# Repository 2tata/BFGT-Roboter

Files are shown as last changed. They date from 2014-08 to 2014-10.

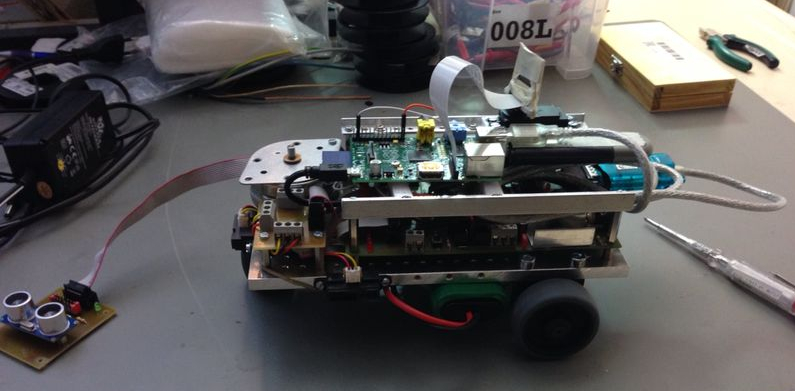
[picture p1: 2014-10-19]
Documentation/Hans Riegel Preis/images/image_47.jpeg

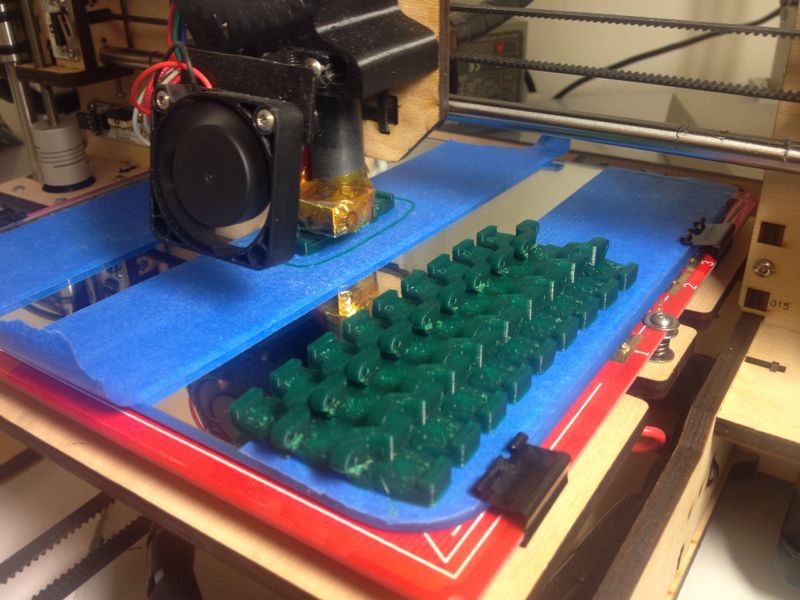
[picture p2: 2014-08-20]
Bilder/BFGT-Roboter_v2/IMG_0849.JPG

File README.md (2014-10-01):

BFGT-Roboter
============

##### ToDo

###### ATmega32
1.Ultraschall-Sensor Funktion inplementieren	  <-- Done, testing

2.Schrittmotor Funktion inplementieren	      	<-- Done, testing

3.Schrittmotor endstop Funktion inplementiren	<-- Done, testing

4.IR Sensoren Funktion korigiren(inplementiren)<-- Done

5.Powersavemode überarbeiten und prüfen	      <-- Done

###### Serial interface
6.Serial daten übertragung optimiren (möglichts kleine und wenige daten)

7.Motor checksum prüfung

###### Raspberry Pi
8.Installations skript coden

9.Open wlan detecter coden

10.Kammera Stream optimiren

11.Servo Steuerung in C

12.Steuerung optimiren

13.Infrarot Leds um die Kamera setzen und über einen Transistor dimbar machen.

14.(OpenCV personen erkennung)

15.Mikrofon audio übertragung

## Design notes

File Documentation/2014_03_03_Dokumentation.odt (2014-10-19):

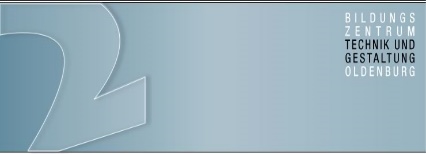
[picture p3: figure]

| Projektkurs - Dokumentation | Schüler: Theis Ammermann, Jan-Tarek Butt, Tobias Beyer, Sören Janke | Klassse: BFI 2
| | | Datum: 11.03.2014

Inhaltsverzeichnis:

1. Einleitung
1. Projektdurchführung
2. Reflexion
3. Literaturverzeichnis
4. Anhang
  a. Protokoll
  b. Zusätzliches Material

Einleitung:

Das Ziel war es, den Mikrocontroller des BZTG's über WLAN/UMTS anzusteuern. Um das sichtbar zu machen, wurde der Mikrocontroller mit Rädern ausgestattet, sodass man ihn über das Internet als eine Art ferngesteuertes Auto ansteuern kann. Das Auto soll vorwärts, rückwärts, nach links und nach rechts fahren können. Der Mikrocontroller wird mit einem Raspberry PI ausgestattet, um mit diesem bestimmte Feature, unter anderem auch die Ansteuerung über das Internet zu ermöglichen.

Erfahrungen hat unsere Gruppe bereits reichlich gesammelt, jeder aus der Gruppe hat Grundkenntnisse in der passenden Programmiersprache „AVR Studio 6“, allerdings gibt es hier natürlich Aufteilungen in unserer Gruppe, den die einen sind gut im Programmieren und die anderen haben bessere Erfahrungen im Bereich deutsch, was bei der Dokumentation hilft.

Das Projekt wird zum Teil außerhalb des Unterrichts bearbeitet. In dem Fach Projektkurs, welches 2-mal pro Woche belegt wird, werden organisatorische Besprechungen und Planungen durchgeführt, außerdem wird an der Dokumentation und an der Programmierung gearbeitet. Außerhalb des Unterrichts werden zum Beispiel Komponenten zum Mikrocontroller hinzugefügt.

Als Software verwenden wir „AVR STUDIO 6.1“ zur „C“ Programmierung des Mikrocontrollers, des weiteren wurden auf dem Raspberry PI die Programmiersprache „Python“ und die Script-Sprache „Bash“ verwendet. Zum Festhalten der Protokolle und der Dokumentation verwendeten wir Microsoft Word und Libre Office. Zum Erstellen der Projektstrukturpläne haben wir DIA verwendet.

Die Aufgaben Verteilung sah folgender maßen aus, Jan-Tarek Butt und Garrit Garre befassten sich hauptsächlich mit der Programmierung des Mikrocontrollers. Sören Janke und Tobias Beyer befasste sich größtenteils mit der Gestaltung der Projektstrukturpläne. Theis Ammermann beschäftigte sich Grundsätzlich mit der Fertigstellung der Dokumentation. Für die Fertigstellung der Protokolle setzten sich Jan-Tarek Butt, Garrit Garre und Theis Ammermann.

Um das Projekt durchführen zu können wird ein Mikrocontroller benötigt, der zu einem Fahrzeug umfunktioniert wurde. Außerdem wird ein Raspberry PI vorausgesetzt und ein Rechner. Optional wird ein vServer im Internet benötigt um den µC über das UMTS Netz zu steuern.

Ein TCP gesteuerter Mikrocontroller der mit Hilfe von einer Netzwerkverbindungen gesteuert werden kann. Des weiteren gibt es eine Infrarot-Videoübertragung, ein Ultraschallradar und Infrarot Distanzsensoren.

Durchführung des Projektes:

Am Anfang des Projektes wurde eine ToDo-Liste(siehe Anhang 1) erstellt. Im Anschluss wurde dann eine darauf basierende Vorgangs-liste(siehe Anhang 2) geschrieben, welche Stück für Stück abgearbeitet wurden. Außerdem wurde die Vorgangs-liste auf einen Projektstrukturplan(siehe Anhang 3) übertragen, in welchem die Vorgänge in Kategorien eingeteilt wurden und letztendlich auch auf einen Terminplan übertragen wurden.

Der Terminplan wurde mit MS-Project angefertigt, wodurch auch automatisch ein Netzplan erzeugt wurde. Dieser wurde danach als Bild exportiert und soweit es ging komprimiert.

Da das Team schon für einige vorherige Projekte Terminpläne angelegt hat, war dieses bereits mit der Verwendung des Programms und dem Ablauf der Erzeugung vertraut.

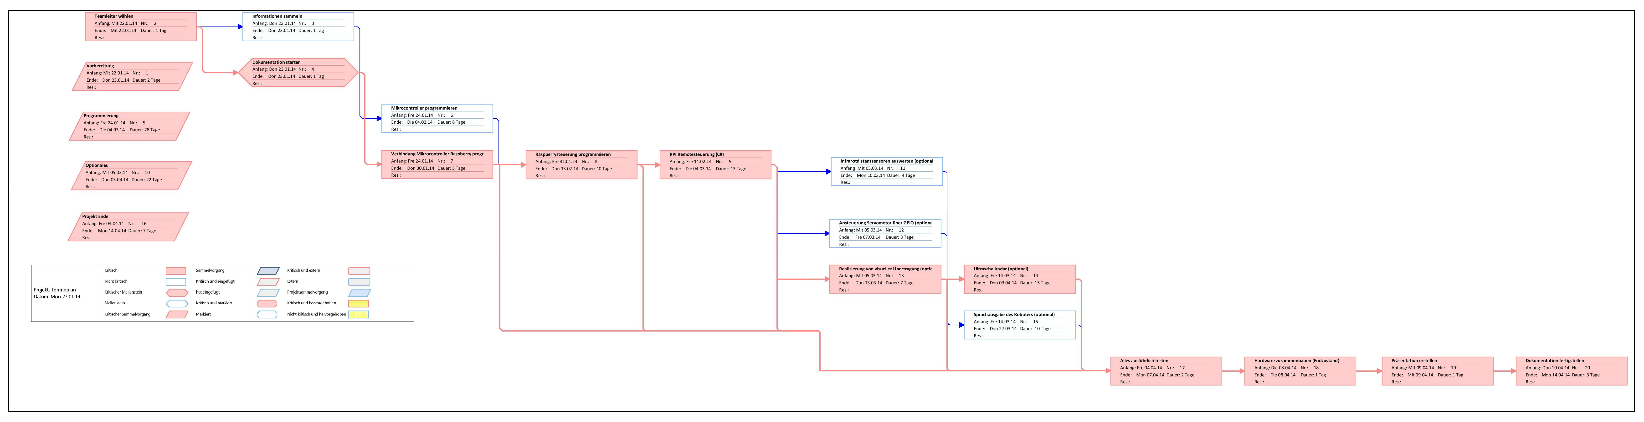
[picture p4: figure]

Für dieses Projekt gibt es Grundlagen, vor allem die C-Programmierung und der allgemeine Umgang mit dem Mikrocontroller. Es gibt bereits Erfahrung mit der Programmierung eines zum Auto umfunktionierten Mikrocontrollers, da dies mal ein Arbeitsauftrag im Unterricht „Technische Projekte“ war.

Das Ziel des Projektes ist es, den Mikrocontroller „ATmega32“ in Form eines Autos mit einigen Zusatzfeatures mithilfe eines Raspberry PI über WLAN anzusteuern.

Der Gruppe wurde von der Schule ein bereits zum Fahrzeug umfunktionierter Mikrocontroller zur Verfügung gestellt. Dieser wurde nach und nach mit neuen Bauteilen versehen. Als erstes kam der Raspberry PI, der den Kontakt vom Mikrocontroller zum Internet überhaupt erst möglich macht. An einem USB-Port wurde eine WLAN-Karte angebracht. Außerdem wurde eine Kamera zur Bildübertragung per Flachbandkabel angeschlossen.

Als dies abgeschlossen war, wurden Infrarot-Sensoren links, rechts und an der Hinterseite des Fahrzeugs angebracht und auf dem Fahrzeug befindet sich ein Schrittmotor woran ein Ultraschallsensor angebracht ist.

Im Folgenden kommen einige Berechnungen zu Funktions Annäherung und Filterung Der Infrarot-Distanzsensoren :

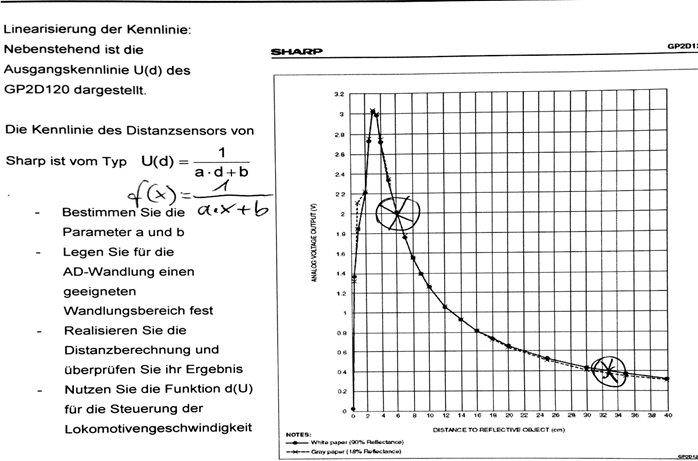
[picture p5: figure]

Kennlinie der Sharp Infrarot Sensoren

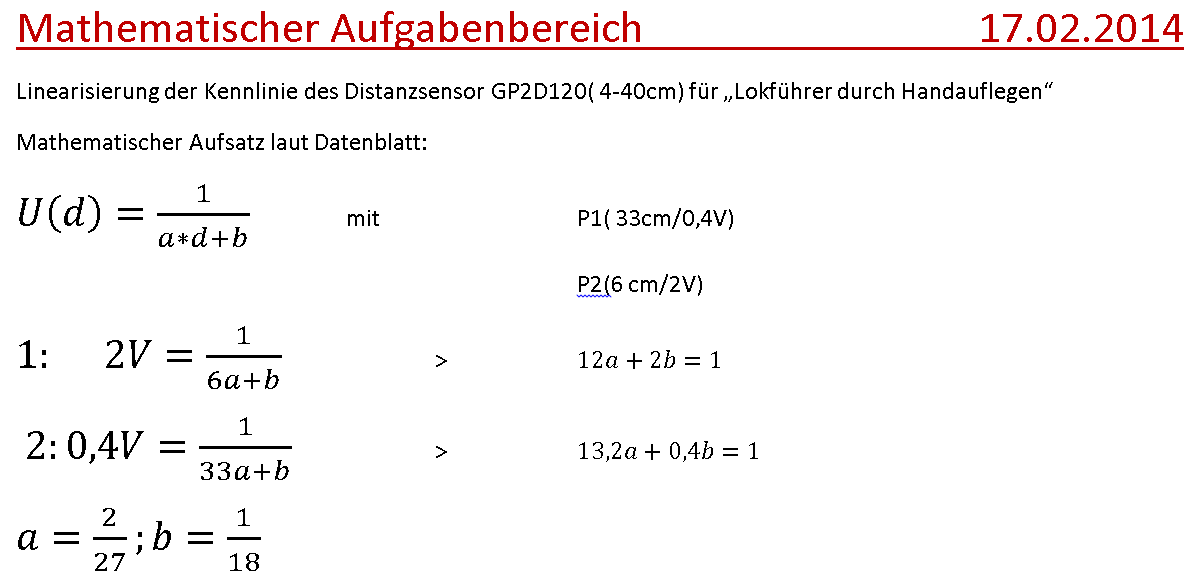
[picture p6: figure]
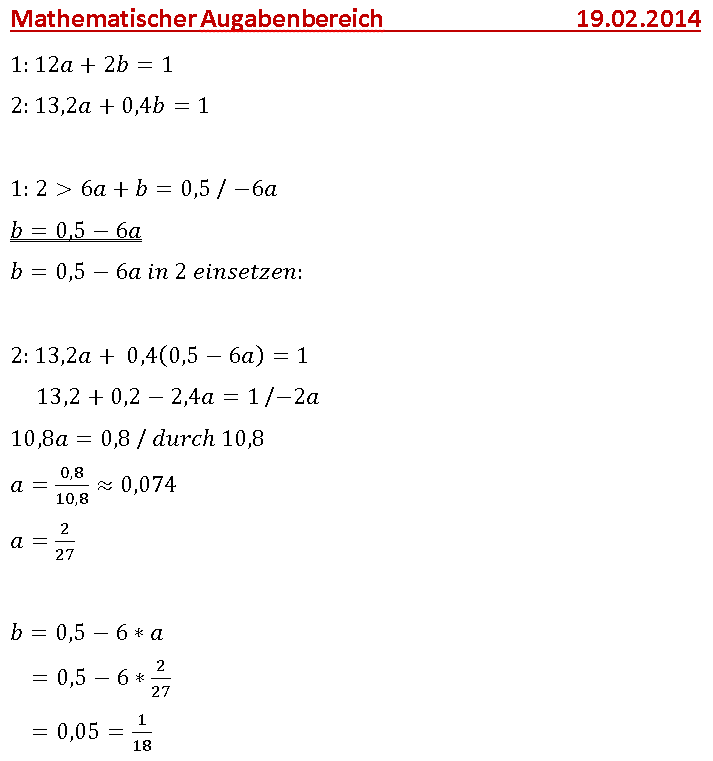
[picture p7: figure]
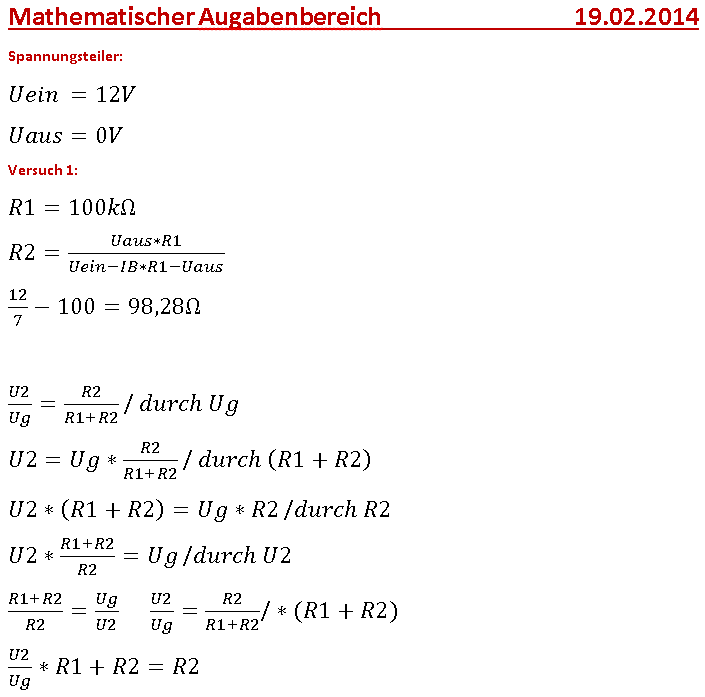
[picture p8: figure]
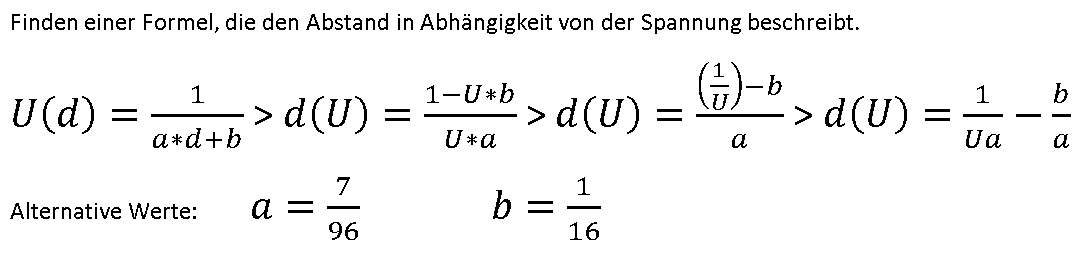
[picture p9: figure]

Entwicklung dess Protokols zwischen Raspberry PI und ATmega32:

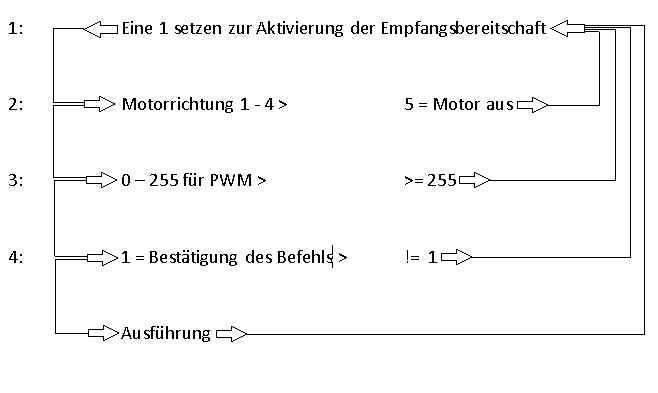
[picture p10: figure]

Um eine Datenübertragung zu starten wird eine 50-49 (ASCII-Zeichen == 1) gesendet. Anschließend Wartet der ATmega32 auf 2 Zeichen zwischen 1-5 für den Motor zustand. Darauf hin sendet man zweimal eine wert zwischen 0-255 für das PWM was die Geschwindigkeit der Motoren regelt. Sobald man die PWM werte gesetzt hat senden der Mikrocontroller die werte zurück, wenn die werte äquivalent zu den eingegebenen werten sind wird eine 1 gesendet was vergleichbar mit einen ACK-Byte ist. Daraufhin führt der ATmega32 sein Befehl aus.

Monolithischer Aufbau der Software Ebenen:

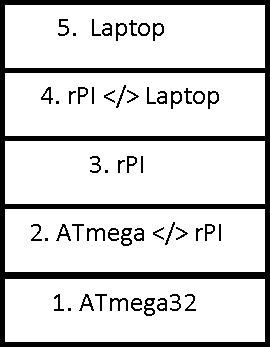
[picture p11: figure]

Kommunikation zwischen Raspberry PI und Laptop

rPI ist zu verstehen als Raspberry PI

Kommunikation zwischen ATmega32 und Raspberry PI

Port Belegung des ATmega32's:

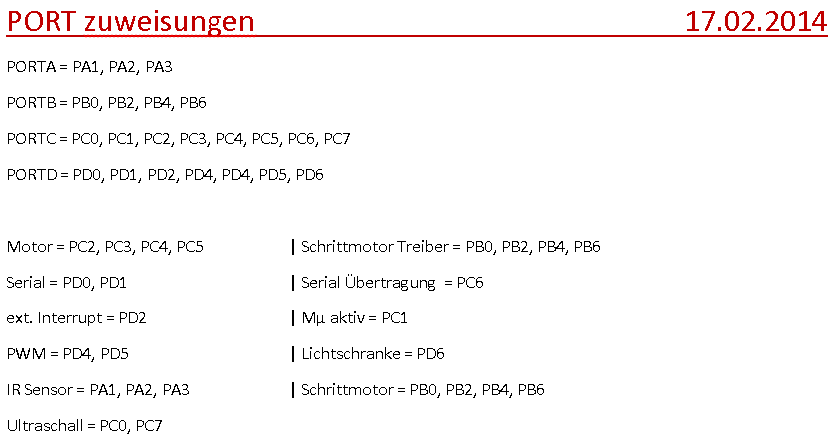
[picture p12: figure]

3. Reflexion:

Das Projekt lief sehr gut und es ging sehr schnell voran, da schon Erfahrung bei der Programmierung in der Gruppe vorhanden war. Aber auch bei der Programmierung gab es Probleme, da keiner der Gruppenmitglieder ausreichende Ahnung mit der Ultraschallprogrammierung hatte. Nach längerem Suchen im Internet und austesten wurde das Problem jedoch gelöst. Im Integrieren der Ultraschallsensoren gab es die meisten Probleme auf Grund der unerfahrenen Bearbeitung, hier drin lag das größte aber nicht das einzige Problem. Es gab noch viele kleinere Probleme wie z.B. die Ansteuerung der Infrarotsensoren, aber die wurden schnell gelöst.

Obwohl das Projekt sehr viele Funktionen hat, ist es noch erweiterbar und offen für viele weitere Funktionen.

Zukünftige Projekte?

Ein weiteres Projekt könnte eine Oberflächen Bearbeitung beinhalten indem ein Kettenantrieb und eine Abdeckung der Hardware angebracht werden

können.

Erweiterungsmöglichkeiten?

Das Projekt könnte durch eine Erweiterung durch eine C# programmierte Oberfläche einfacher zu steuern und auch in Sachen Design ein höheren Stellenwert haben. Unter anderem könnte man eine Personen und Gesten Erkennung Implementieren.

Andere Lösungsansätze?

Es bestehen keine anderen Lösungsansätze.

4.Literaturverzeichnis:

Quellenangabe:

http://raspberrypiguide.de/howtos/raspberry-pi-gpio-how-to/

http://www.roboternetz.de/community/threads/62655-Raspberry-Pi-mit-Vb-net

http://www.mydealz.de/25645/raspberry-pi-modell-b-fur-30e-mini-rechner-zum-basteln/

https://www.google.com/search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

http://www.rasppishop.de/raspberry-pi-welt/erweiterungen/1/raspberry-pi-model-b-512mb-ram-rev.-2.0

https://github.com/2tata/BFGT-Roboter/blob/master/BFGTmega32-Board/Roboter.c

http://www.thingiverse.com/thing:36305/#files

http://markslaboratory.com/2013/04/mirroring-an-stl-for-makerware/

http://kampis-elektroecke.de/?page_id=3066

http://pymotw.com/2/socket/tcp.html

http://ipv6friday.org/blog/2011/11/ipv6addresses/

5.Anhang:

Protokolle:

Lfd. Nr. : 1 | Protokoll | Bemerkungen:

Arbeitsgruppe: Gruppenthema: | Tarek, Sören, Tobias, Theis, Garrit µC über Internet
Zeit / Ort: Anwesende: | 09:15 Oldenburg (im BZTG) Tarek, Sören, Tobias, Garrit
Ziel(e) der Sitzung? | Findung vom Projekt
1. Verlauf | Besprechung der Möglichkeiten, Ideen sammeln,
2. Ergebnisse | Folgende Projekt Möglichkeiten: µC Ethernet Steuerung, Freifunk 2.0, µC über C# steuern, 3D Drucker/ Scanner
3. Weiterarbeit | Information sammeln, Ordnerstrukturen erstellen

Oldenburg, den 13.01.2014 | Garrit Garre

Lfd. Nr. : 2 | Protokoll | Bemerkungen:

Arbeitsgruppe: Gruppenthema: | Tarek, Sören, Tobias, Theis, Garrit µC über Internet
Zeit / Ort: Anwesende: | 11:15 Oldenburg (im BZTG) Tarek, Tobias, Garrit
Ziel(e) der Sitzung? | Erstellung der ToDo-Liste
1. Verlauf | Besprechung über die Features des µC und wie wir sie umsetzen werden.
2. Ergebnisse | Es wurde eine ToDo-Liste erstellt und festgelegt, was der µC können soll.
3. Weiterarbeit | -Vorgangsliste -OIL anlegen

Oldenburg, den 15.01.2014 | Tobias Beyer

Lfd. Nr. : 3 | Protokoll | Bemerkungen:

Arbeitsgruppe: Gruppenthema: | Tarek, Sören, Tobias, Theis, Garrit µC über Internet
Zeit / Ort: Anwesende: | 09:20 Oldenburg (im BZTG) Tarek, Sören, Tobias
Ziel(e) der Sitzung? | Vorgangsliste und Programmierung
1. Verlauf | Sammlung von Vorgängen, Ideen zur Programmierung
2. Ergebnisse | Fertigstellung der Vorgangsliste, Prototyp des Programmes, Erstellung der OIL.
3. Weiterarbeit | Terminplanung, Projektstrukturplan erstellen, OIL aktualisieren.

Oldenburg, den 20.01.2014 | Sören Janke

Lfd. Nr. : 4 | Protokoll | Bemerkungen:

Arbeitsgruppe: Gruppenthema: | Tarek, Sören, Tobias, Theis, Garrit µC über Internet
Zeit / Ort: Anwesende: | 11:12 Oldenburg (im BZTG) Tarek, Sören, Tobias, Garrit
Ziel(e) der Sitzung? | Projektstrukturplan und Programmierung
1. Verlauf | Sammlung von Vorgängen, Ideen zur Programmierung
2. Ergebnisse | Fertigstellung des Projektstrukturplans, Terminplan wurde erstellt.
3. Weiterarbeit | Terminplan aktualisieren, OIL aktualisieren, mit Programmierarbeit fortfahren.

Oldenburg, den 22.01.2014 | Tobias Beyer

Lfd. Nr. : 5 | Protokoll | Bemerkungen:

Arbeitsgruppe: Gruppenthema: | Tarek, Sören, Tobias, Theis, Garrit µC über Internet
Zeit / Ort: Anwesende: | 09:23 Oldenburg (im BZTG) Tarek, Tobias
Ziel(e) der Sitzung? | -Terminplan überarbeiten, -Servoansteuerung implementieren
1. Verlauf | Sammlung von Vorgängen, Ideen zur Programmierung
2. Ergebnisse | - Terminplan wurde überarbeitet und als JPG gespeichert
3. Weiterarbeit | Fahrzeugbau

Oldenburg, den 27.01.2014 | Tobias Beyer

Lfd. Nr. : 6 | Protokoll | Bemerkungen:

Arbeitsgruppe: Gruppenthema: | Tarek, Sören, Tobias, Theis, Garrit µC über Internet
Zeit / Ort: Anwesende: | 09:12 Oldenburg (im BZTG) Tarek, Tobias, Garrit, Theis
Ziel(e) der Sitzung? | Den Roboter energieeffizienter programmieren, an der Dokumentation arbeiten
1. Verlauf | Sammlung von Vorgängen, Ideen zur Programmierung
2. Ergebnisse | Fahrzeug wurde erweitert, Start der Dokumentation
3. Weiterarbeit | Dokumentation ausarbeiten, neue Fahrzeug teile integrieren

Oldenburg, den 03.02.2014 | Tobias Beyer

Lfd. Nr. : 7 | Protokoll | Bemerkungen:

Arbeitsgruppe: Gruppenthema: | Tarek, Sören, Tobias, Theis, Garrit µC über Internet
Zeit / Ort: Anwesende: | 10:58 Oldenburg (im BZTG) Tarek, Tobias, Garrit, Theis
Ziel(e) der Sitzung? | Den Roboter energieeffizienter programmieren
1. Verlauf | Sammlung von Vorgängen, Ideen zur Programmierung
2. Ergebnisse | Der Roboter wurde energieeffizienter programmiert.
3. Weiterarbeit | Raspberry integrieren

Oldenburg, den 05.02.2014 | Tobias Beyer

Lfd. Nr. : 8 | Protokoll | Bemerkungen:

Arbeitsgruppe: Gruppenthema: | Tarek, Sören, Tobias, Theis, Garrit µC über Internet
Zeit / Ort: Anwesende: | 09:10 Oldenburg (im BZTG) Tarek, Tobias, Garrit, Theis, Sören
Ziel(e) der Sitzung? | Serielles Protokoll implementieren
1. Verlauf | Sammlung von Vorgängen, Ideen zur Programmierung
2. Ergebnisse | Raspbarry intigriert Serielles Protokoll wurde implementiert
3. Weiterarbeit | Serielles Protokoll implementieren

Oldenburg, den 10.02.2014 | Tobias Beyer

Lfd. Nr. : 9 | Protokoll | Bemerkungen:

Arbeitsgruppe: Gruppenthema: | Tarek, Sören, Tobias, Theis, Garrit µC über Internet
Zeit / Ort: Anwesende: | 11:09 Oldenburg (im BZTG) Tarek, Tobias, Theis
Ziel(e) der Sitzung? | Den Schrittmotor einbauen
1. Verlauf | Sammlung von Vorgängen, Ideen zur Programmierung
2. Ergebnisse | Serielles Protokoll implementiert
3. Weiterarbeit | Schrittmotor intrigieren

Oldenburg, den 12.02.2014 | Tobias Beyer

Lfd. Nr. : 10 | Protokoll | Bemerkungen:

Arbeitsgruppe: Gruppenthema: | Tarek, Sören, Tobias, Theis, Garrit µC über Internet
Zeit / Ort: Anwesende: | 08:56 Oldenburg (im BZTG) Tarek, Tobias, Theis
Ziel(e) der Sitzung? | An der Dokumentation weiterarbeiten, die Benennung der Protokoll-Dateien verbessern
1. Verlauf | Sammlung von Vorgängen, Ideen zur Programmierung
2. Ergebnisse | Schrittmotor weiterbau, OIL
3. Weiterarbeit | Raspberry erweitern

Oldenburg, den 17.02.2014 | Tobias Beyer

Lfd. Nr. : 11 | Protokoll | Bemerkungen:

Arbeitsgruppe: Gruppenthema: | Tarek, Sören, Tobias, Theis, Garrit µC über Internet
Zeit / Ort: Anwesende: | 08:56 Oldenburg (im BZTG) Tarek, Tobias, Theis
Ziel(e) der Sitzung? | An der Dokumentation weiterarbeiten
1. Verlauf | Sammlung von Vorgängen, Ideen zur Programmierung
2. Ergebnisse | Infrarot-Distanz-Sensor anbauen
3. Weiterarbeit | OIL aktualisieren, Programmierarbeit fortsetzen.

Oldenburg, den 19.02.2014 | Tobias Beyer

Lfd. Nr. : 12 | Protokoll | Bemerkungen:

Arbeitsgruppe: Gruppenthema: | Tarek, Sören, Tobias, Theis, Garrit µC über Internet
Zeit / Ort: Anwesende: | 08:56 Oldenburg (im BZTG) Tarek, Tobias, Theis
Ziel(e) der Sitzung? | Infrarot-Distanz-Sensor
1. Verlauf | Sammlung von Vorgängen, Ideen zur Programmierung
2. Ergebnisse | Programmierung Infrarot-Distanz-Sensor
3. Weiterarbeit | Zusammensetzung der Dokumentation

Oldenburg, den 24.02.2014 | Tobias Beyer

Lfd. Nr. : 13 | Protokoll | Bemerkungen:

Arbeitsgruppe: Gruppenthema: | Tarek, Sören, Tobias, Theis, Garrit µC über Internet
Zeit / Ort: Anwesende: | 08:56 Oldenburg (im BZTG) Tarek, Tobias, Theis
Ziel(e) der Sitzung? | An der Dokumentation weiterarbeiten
1. Verlauf | Sammlung von Vorgängen, Ideen zur Programmierung
2. Ergebnisse | Dokumentation erweitert
3. Weiterarbeit | Dokumentation erweitern

Oldenburg, den 26.02.2014 | Tobias Beyer

Lfd. Nr. : 14 | Protokoll | Bemerkungen:

Arbeitsgruppe: Gruppenthema: | Tarek, Sören, Tobias, Theis, Garrit µC über Internet
Zeit / Ort: Anwesende: | 08:56 Oldenburg (im BZTG) Tarek, Tobias, Theis
Ziel(e) der Sitzung? | An der Dokumentation weiterarbeiten
1. Verlauf | Sammlung von Vorgängen, Ideen zur Programmierung
2. Ergebnisse | Dokumentation erweitert
3. Weiterarbeit | Dokumentation erweitert, OIL , Grundlegendes

Oldenburg, den 03.03.2014 | Tobias Beyer

Lfd. Nr. : 15 | Protokoll | Bemerkungen:

Arbeitsgruppe: Gruppenthema: | Tarek, Sören, Tobias, Theis, Garrit µC über Internet
Zeit / Ort: Anwesende: | 08:56 Oldenburg (im BZTG) Tarek, Tobias, Theis
Ziel(e) der Sitzung? | An der Dokumentation weiterarbeiten, OIL, Grundlegendes
1. Verlauf | Sammlung von Vorgängen, Ideen zur Programmierung
2. Ergebnisse | Es wurde an der Dokumentation geschrieben, Software-Test
3. Weiterarbeit | Dokumentation abschließen, Allgemeine Tests und Überprüfung der Dateien

Oldenburg, den 05.03.2014 | Tobias Beyer

Lfd. Nr. : 16 | Protokoll | Bemerkungen:

Arbeitsgruppe: Gruppenthema: | Tarek, Sören, Tobias, Theis, Garrit µC über Internet
Zeit / Ort: Anwesende: | 08:56 Oldenburg (im BZTG) Tarek, Tobias, Theis
Ziel(e) der Sitzung? | An der Dokumentation fertigstellen, Allgemeine Tests
1. Verlauf | Sammlung von Vorgängen, Ideen zur Programmierung
2. Ergebnisse | Dokumentation fertigstellen, Präsentation erstellen, Abschluss-Tests
3. Weiterarbeit | Abgabe

Oldenburg, den 10.03.2014 | Tobias Beyer

Zusätzliches Material:

Todo-liste:(Anhang 1)

Stepp 1 Mikrocontroler

Was soll der Mikrocontroler können?

- I/O Steuerung

- ADW Steuerung

- PWM Steuerung

-I2C Steuerung

Stepp 2 Microcontroler > Rassberry Pi

Wie soll der Microcontroler gesteuert werden?

- GPI/O Pins

- Serielle Steuerung

- I2C Steuerung

- JTAG Steuerung

Stepp 3 Rasberry Pi steuerung

Was soll der Rasberry können?

- Remoute Schnittstelle spielen

- Server spielen

- Protokoll Sockel bilden

- Viertual Serial Com emulirung

- SFTP Server

- Netcat

- SSH

- TCP-/IP-Stack

- ?

Stepp 4 Rasberry Pi remoute Steuerung

Wie soll der Rasberry gesteuert werden Windows/Linux?

- C# Programm (Windows)

- Webinterface (OS unabhängig)

- C Programm (Linux)

- Java Programm (Windows und Linux)

- (Video Stream Implementierung ins Programm)

Vorgangs-liste:(Anhang 2)

Nr. | Vorgang | Dauer (Tage) | Vorgänger
1 | Teamleiter wählen✔ | 1 | -
2 | Informationen sammeln✔ | 1 | 1
3 | Dokumentation starten✔ | M | 1
4 | Mikrocontroller programmieren✔ | 8 | 3
5 | Verbindung mit Mikrocontroller und Raspberry Pi programmieren✔ | 5 | 3
6 | Raspberrysteuerung programmieren✔ | 10 | 5
7 | RPI Remotesteuerung (C#) (optional) | 13 | 6
8 | Infrarotdistanzsensoren auswerten (optional)✔ | 4 | 7
9 | Ansteuerung Servomotor über GPIO (optional)✔ | 3 | 7
10 | Realisierung von visueller Übertragung (optional)✔ | 7 | 7
11 | Ultraschallradar (optional)✔ | 15 | 10
12 | Sprachausgabe des Roboters (optional) | 10 | 10
13 | Alles ausführlich testen✔ | 2 | 4-12
14 | Hardware zusammenbauen (Endzustand)✔ | 1 | 13
15 | Präsentation erstellen✔ | 1 | 14
16 | Dokumentation fertigstellen✔ | 3 | 15

Projektstrukturplan:(Anhang 3)

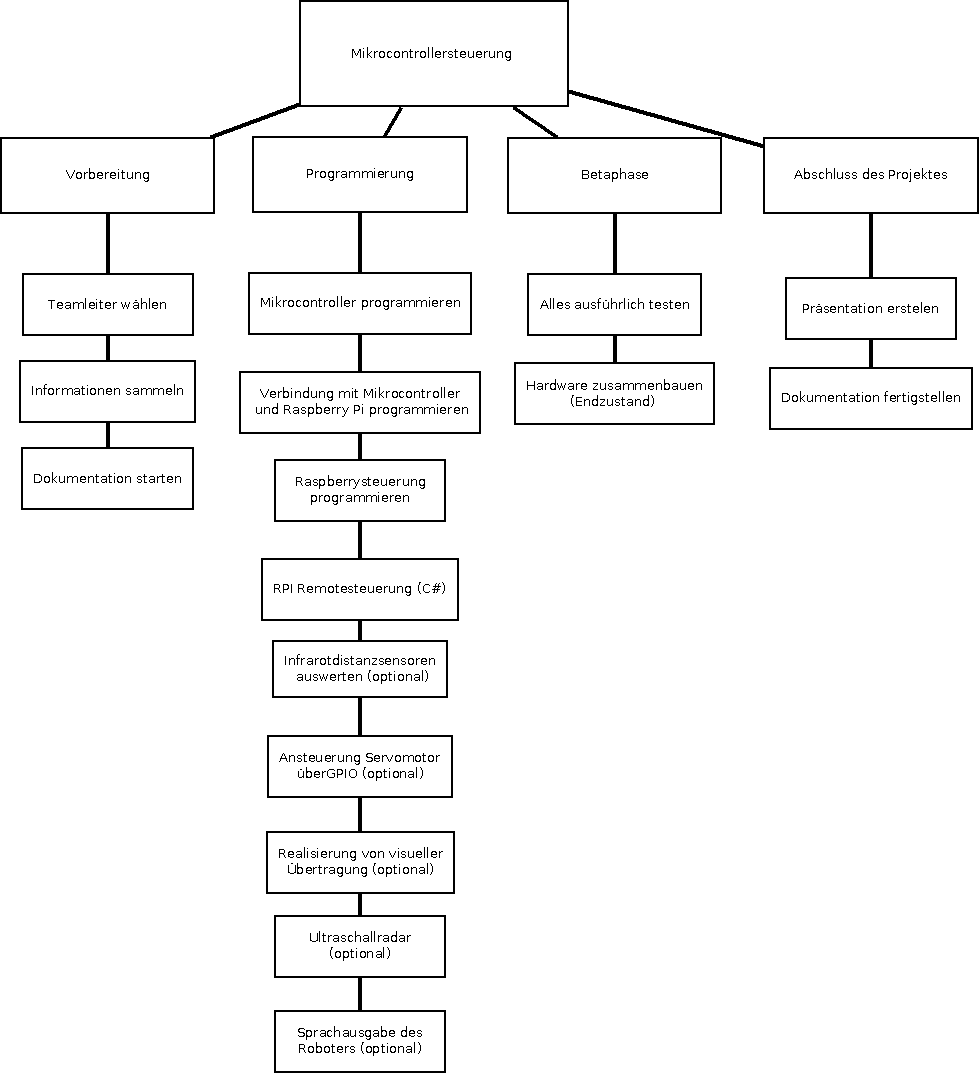
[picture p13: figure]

Dokumentation Mikrocontroller über Ethernet

Projektkurs: microcontroller über ethernet Theis Ammermann, Jan-tarek butt. sören j,tobias b 27

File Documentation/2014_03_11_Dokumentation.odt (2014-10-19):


| Projektkurs - Dokumentation | Schüler: Theis Ammermann, Jan-Tarek Butt, Garrit Garre, Tobias Beyer, Sören Janke | Klassse: BFI 2
| | | Datum: 11.03.2014

Inhaltsverzeichnis:

1. Einleitung
1. Projektdurchführung
  a. Infrarot-Distanzsensoren
  b. Ultraschall Sensor
  c. Protokoll Entwicklung
2. Reflexion
3. Literaturverzeichnis
4. Anhang
  a. Protokoll
  b. Code
  c. Zusätzliches Material

Einleitung:

Das Ziel war es, den Mikrocontroller „BFGTmega32“ des BZTG's über WLAN/UMTS anzusteuern. Um das sichtbar zu machen, wurde der Mikrocontroller mit Rädern ausgestattet, sodass man ihn über das Internet als eine Art ferngesteuerten Roboter ansteuern kann. Der Roboter soll vorwärts, rückwärts, nach links und nach rechts fahren können. Der Mikrocontroller wird mit einem Raspberry PI ausgestattet, dieser Bildet die Schnittstelle zur Ansteuerung über das Internet oder Lokale Netzwerk.

Unsere Gruppe hat bereits viele Erfahrungen in unterschiedlichen Bereichen. Theis Ammermann Besitzt gute Kenntnisse im Bereich Design und Dokumentation. Jan-Tarek Butt hat sehr gute Kenntnisse in den Programmiersprachen C, Python und Bash was für die Programmierung des Roboters Notwendig war. Zusätzlich Besitzt Jan-Tarek Butt auch ein umfangreiches Wissen über das Betriebssystem Linux, welchen auf dem Raspbarry PI zum Einsatz kam. Garrit Garre Besitz zusätzlich sehr gute solide Kenntnisse in der C Programmierung für den Mikrocontroller. Tobias Beyer und Sören Janke haben viel Erfahrungen in Protokollierung und in Projekt Strukturierung was Zeit-Management mit ein beschließt. Somit konnten wir eine Relativ optimierte Aufgaben Verteilung erzielen.

Das Projekt wird zum Teil außerhalb des Unterrichts bearbeitet. In dem Fach Projektkurs, welches 2-mal pro Woche belegt wird, werden organisatorische Besprechungen und Planungen durchgeführt, außerdem wird an der Dokumentation und an der Programmierung gearbeitet. Außerhalb des Unterrichts werden zum Beispiel Komponenten zum Mikrocontroller hinzugefügt.

Als Software verwenden wir „AVR STUDIO 6.1“ zur „C“ Programmierung des Mikrocontrollers, des weiteren wurden auf dem Raspberry PI die Programmiersprache „Python“ und die Script-Sprache „Bash“ verwendet. Zum Festhalten der Protokolle und der Dokumentation verwendeten wir Libre Office. Zum Erstellen der Projektstrukturpläne und des Flussdiagramms (siehe Anhang 1) haben wir DIA verwendet.

Die Aufgaben Verteilung sah folgender maßen aus, Jan-Tarek Butt und Garrit Garre befassten sich hauptsächlich mit der Programmierung des Mikrocontrollers. Sören Janke und Tobias Beyer befasste sich größtenteils mit der Gestaltung der Projektstrukturpläne. Theis Ammermann beschäftigte sich Grundsätzlich mit der Fertigstellung der Dokumentation. Für die Fertigstellung der Protokolle sorgten Jan-Tarek Butt, Garrit Garre und Theis Ammermann.

Um das Projekt durchführen zu können wird ein Mikrocontroller benötigt, der zu einem Fahrzeug umfunktioniert wurde. Außerdem wird ein Raspberry PI vorausgesetzt und ein Rechner. Optional wird ein vServer im Internet benötigt um den µC über das UMTS Netz zu steuern.

Der Mikrocontroller wird über das TCP Protokoll mit Hilfe von einer Netzwerkverbindungen gesteuert. Des weiteren gibt es eine Infrarot-Videokamera, ein Ultraschall-Radar und Infrarot-Distanzsensoren.

Durchführung des Projektes:

Am Anfang des Projektes wurde eine ToDo-Liste(siehe Anhang 2) erstellt. Im Anschluss wurde dann eine darauf basierende Vorgangs-liste(siehe Anhang 3) geschrieben, welche Stück für Stück abgearbeitet wurden. Außerdem wurde die Vorgangs-liste auf einen Projektstrukturplan(siehe Anhang 4) übertragen, in welchem die Vorgänge in Kategorien eingeteilt wurden und letztendlich auch auf einen Terminplan übertragen wurden.

Der Terminplan wurde mit MS-Project angefertigt, wodurch auch automatisch ein Netzplan erzeugt wurde. Dieser wurde danach als Bild exportiert und soweit es ging komprimiert.

Da das Team schon für einige vorherige Projekte Terminpläne angelegt hat, war dieses bereits mit der Verwendung des Programms und dem Ablauf der Erzeugung vertraut.


Für dieses Projekt gibt es Grundlagen, vor allem die C-Programmierung und der allgemeine Umgang mit dem Mikrocontroller. Es gibt bereits Erfahrung mit der Programmierung eines zum Auto umfunktionierten Mikrocontrollers, da dies mal ein Arbeitsauftrag im Unterricht „Technische Prozesse“ war.

Das Ziel des Projektes ist es, den Mikrocontroller „ATmega32“ in Form eines Roboters mit einigen Sensoren mithilfe eines Raspberry PI über WLAN anzusteuern.

Der Gruppe wurde von der Schule ein bereits zum Fahrzeug umfunktionierter Mikrocontroller zur Verfügung gestellt. Dieser wurde nach und nach mit neuen Bauteilen versehen. Als erstes kam der Raspberry PI, der den Kontakt vom Mikrocontroller zum Internet überhaupt erst möglich macht. An einem USB-Port wurde eine WLAN-Karte angebracht. Außerdem wurde eine Kamera zur Bildübertragung per Flachbandkabel angeschlossen.

Als dies abgeschlossen war, wurden Infrarot-Sensoren links, rechts und an der Hinterseite des Fahrzeugs angebracht und auf dem Fahrzeug befindet sich ein Schrittmotor woran ein Ultraschallsensor angebracht ist.

Im Folgenden kommen einige Berechnungen zu Funktions Annäherung und Filterung Der Infrarot-Distanzsensoren :


Kennlinie der Sharp Infrarot Sensoren


Ultraschall Sensor

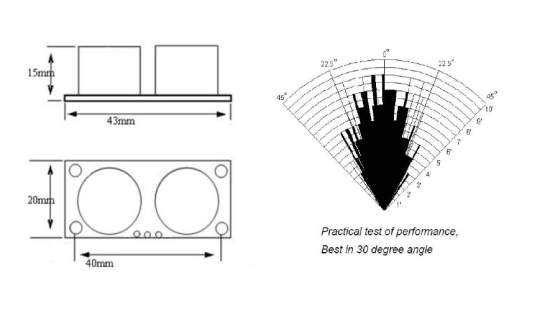
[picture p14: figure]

Der Ultraschall Sensor hat einen Unfairen Öffnungswinkel von 30°. Die Bauform ist den oberen Bild zu entnehmen.

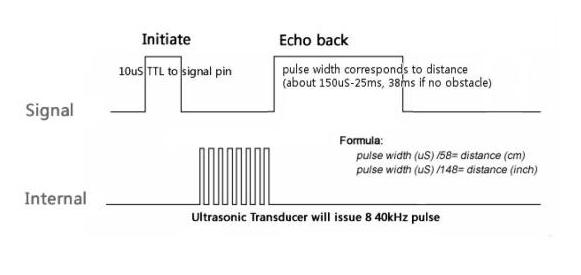
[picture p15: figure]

Die Ansteuerung des Ultraschall Sensors ist Relativ Komplex. Man muss ein ca. 10 µs Sekunden langes Signal auf den Trigger-Pin legen und bekommt ein Echo Signal auf dem Echo-Pin zurück. Die Länge des Echosignals wird mit einen Timer gemessen, da die Länge mit der gemessenen Distanz des Sensors variiert.

Entwicklung des Protokolls zwischen Raspberry PI und ATmega32:


Um eine Datenübertragung zu starten wird eine 50-49 (ASCII-Zeichen == 1) gesendet. Anschließend Wartet der ATmega32 auf 2 Zeichen zwischen 1-5 für den Motor zustand. Darauf hin sendet man zweimal eine wert zwischen 0-255 für das PWM was die Geschwindigkeit der Motoren regelt. Sobald man die PWM werte gesetzt hat senden der Mikrocontroller die werte zurück, wenn die werte äquivalent zu den eingegebenen werten sind wird eine 1 gesendet was vergleichbar mit einen ACK-Byte ist. Daraufhin führt der ATmega32 sein Befehl aus.

Monolithischer Aufbau der Software Ebenen:


Kommunikation zwischen Raspberry PI und Laptop

rPI ist zu verstehen als Raspberry PI

Kommunikation zwischen ATmega32 und Raspberry PI

Port Belegung des ATmega32's:


3. Reflexion:

Das Projekt lief sehr gut und es ging sehr schnell voran, da schon Erfahrung bei der Programmierung in der Gruppe vorhanden war. Aber auch bei der Programmierung gab es Probleme, da keiner der Gruppen Mitglieder ausreichende Ahnung mit der Ultraschall Sensor Programmierung hatte. Nach längerem Suchen im Internet und austesten wurde das Problem jedoch gelöst. Im Integrieren des Ultraschallsensors gab es die meisten Probleme auf Grund der unerfahrenen Bearbeitung, hier drin lag das größte aber nicht das einzige Problem. Es gab noch viele kleinere Probleme wie z.B. die Ansteuerung der Infrarot-Sensoren, aber die wurden schnell gelöst.

Obwohl das Projekt sehr viele Funktionen hat, ist es noch erweiterbar und offen für viele weitere Funktionen.

Zukünftige Projekte?

Ein weiteres Projekt könnte eine Oberflächen Bearbeitung beinhalten indem ein Kettenantrieb und eine Abdeckung der Hardware angebracht werden

können.

Erweiterungsmöglichkeiten?

Das Projekt könnte durch eine Erweiterung durch eine C# programmierte Oberfläche einfacher zu steuern und auch in Sachen Design ein höheren Stellenwert haben. Unter anderem könnte man eine Personen und Gesten Erkennung Implementieren.

Andere Lösungsansätze?

Es bestehen keine anderen Lösungsansätze.

4.Literaturverzeichnis:

Quellenangabe:

http://raspberrypiguide.de/howtos/raspberry-pi-gpio-how-to/

http://www.roboternetz.de/community/threads/62655-Raspberry-Pi-mit-Vb-net

http://www.mydealz.de/25645/raspberry-pi-modell-b-fur-30e-mini-rechner-zum-basteln/

https://www.google.com/search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

http://www.rasppishop.de/raspberry-pi-welt/erweiterungen/1/raspberry-pi-model-b-512mb-ram-rev.-2.0

https://github.com/2tata/BFGT-Roboter/blob/master/BFGTmega32-Board/Roboter.c

http://www.thingiverse.com/thing:36305/#files

http://markslaboratory.com/2013/04/mirroring-an-stl-for-makerware/

http://kampis-elektroecke.de/?page_id=3066

http://pymotw.com/2/socket/tcp.html

http://ipv6friday.org/blog/2011/11/ipv6addresses/

5.Anhang:

Protokolle:

Lfd. Nr. : 1 | Protokoll | Bemerkungen:

Arbeitsgruppe: Gruppenthema: | Tarek, Sören, Tobias, Theis, Garrit µC über Internet
Zeit / Ort: Anwesende: | 09:15 Oldenburg (im BZTG) Tarek, Sören, Tobias, Garrit
Ziel(e) der Sitzung? | Findung vom Projekt
1. Verlauf | Besprechung der Möglichkeiten, Ideen sammeln,
2. Ergebnisse | Folgende Projekt Möglichkeiten: µC Ethernet Steuerung, Freifunk 2.0, µC über C# steuern, 3D Drucker/ Scanner
3. Weiterarbeit | Information sammeln, Ordnerstrukturen erstellen

Oldenburg, den 13.01.2014 | Garrit Garre

Lfd. Nr. : 2 | Protokoll | Bemerkungen:

Arbeitsgruppe: Gruppenthema: | Tarek, Sören, Tobias, Theis, Garrit µC über Internet
Zeit / Ort: Anwesende: | 11:15 Oldenburg (im BZTG) Tarek, Tobias, Garrit
Ziel(e) der Sitzung? | Erstellung der ToDo-Liste
1. Verlauf | Besprechung über die Features des µC und wie wir sie umsetzen werden.
2. Ergebnisse | Es wurde eine ToDo-Liste erstellt und festgelegt, was der µC können soll.
3. Weiterarbeit | -Vorgangsliste -OIL anlegen

Oldenburg, den 15.01.2014 | Tobias Beyer

Lfd. Nr. : 3 | Protokoll | Bemerkungen:

Arbeitsgruppe: Gruppenthema: | Tarek, Sören, Tobias, Theis, Garrit µC über Internet
Zeit / Ort: Anwesende: | 09:20 Oldenburg (im BZTG) Tarek, Sören, Tobias
Ziel(e) der Sitzung? | Vorgangsliste und Programmierung
1. Verlauf | Sammlung von Vorgängen, Ideen zur Programmierung
2. Ergebnisse | Fertigstellung der Vorgangsliste, Prototyp des Programmes, Erstellung der OIL.
3. Weiterarbeit | Terminplanung, Projektstrukturplan erstellen, OIL aktualisieren.

Oldenburg, den 20.01.2014 | Sören Janke

Lfd. Nr. : 4 | Protokoll | Bemerkungen:

Arbeitsgruppe: Gruppenthema: | Tarek, Sören, Tobias, Theis, Garrit µC über Internet
Zeit / Ort: Anwesende: | 11:12 Oldenburg (im BZTG) Tarek, Sören, Tobias, Garrit
Ziel(e) der Sitzung? | Projektstrukturplan und Programmierung
1. Verlauf | Sammlung von Vorgängen, Ideen zur Programmierung
2. Ergebnisse | Fertigstellung des Projektstrukturplans, Terminplan wurde erstellt.
3. Weiterarbeit | Terminplan aktualisieren, OIL aktualisieren, mit Programmierarbeit fortfahren.

Oldenburg, den 22.01.2014 | Tobias Beyer

Lfd. Nr. : 5 | Protokoll | Bemerkungen:

Arbeitsgruppe: Gruppenthema: | Tarek, Sören, Tobias, Theis, Garrit µC über Internet
Zeit / Ort: Anwesende: | 09:23 Oldenburg (im BZTG) Tarek, Tobias
Ziel(e) der Sitzung? | -Terminplan überarbeiten, -Servoansteuerung implementieren
1. Verlauf | Sammlung von Vorgängen, Ideen zur Programmierung
2. Ergebnisse | - Terminplan wurde überarbeitet und als JPG gespeichert
3. Weiterarbeit | Fahrzeugbau

Oldenburg, den 27.01.2014 | Tobias Beyer

Lfd. Nr. : 6 | Protokoll | Bemerkungen:

Arbeitsgruppe: Gruppenthema: | Tarek, Sören, Tobias, Theis, Garrit µC über Internet
Zeit / Ort: Anwesende: | 09:12 Oldenburg (im BZTG) Tarek, Tobias, Garrit, Theis
Ziel(e) der Sitzung? | Den Roboter energieeffizienter programmieren, an der Dokumentation arbeiten
1. Verlauf | Sammlung von Vorgängen, Ideen zur Programmierung
2. Ergebnisse | Fahrzeug wurde erweitert, Start der Dokumentation
3. Weiterarbeit | Dokumentation ausarbeiten, neue Fahrzeug teile integrieren

Oldenburg, den 03.02.2014 | Tobias Beyer

Lfd. Nr. : 7 | Protokoll | Bemerkungen:

Arbeitsgruppe: Gruppenthema: | Tarek, Sören, Tobias, Theis, Garrit µC über Internet
Zeit / Ort: Anwesende: | 10:58 Oldenburg (im BZTG) Tarek, Tobias, Garrit, Theis
Ziel(e) der Sitzung? | Den Roboter energieeffizienter programmieren
1. Verlauf | Sammlung von Vorgängen, Ideen zur Programmierung
2. Ergebnisse | Der Roboter wurde energieeffizienter programmiert.
3. Weiterarbeit | Raspberry integrieren

Oldenburg, den 05.02.2014 | Tobias Beyer

Lfd. Nr. : 8 | Protokoll | Bemerkungen:

Arbeitsgruppe: Gruppenthema: | Tarek, Sören, Tobias, Theis, Garrit µC über Internet
Zeit / Ort: Anwesende: | 09:10 Oldenburg (im BZTG) Tarek, Tobias, Garrit, Theis, Sören
Ziel(e) der Sitzung? | Serielles Protokoll implementieren
1. Verlauf | Sammlung von Vorgängen, Ideen zur Programmierung
2. Ergebnisse | Raspbarry intigriert Serielles Protokoll wurde implementiert
3. Weiterarbeit | Serielles Protokoll implementieren

Oldenburg, den 10.02.2014 | Tobias Beyer

Lfd. Nr. : 9 | Protokoll | Bemerkungen:

Arbeitsgruppe: Gruppenthema: | Tarek, Sören, Tobias, Theis, Garrit µC über Internet
Zeit / Ort: Anwesende: | 11:09 Oldenburg (im BZTG) Tarek, Tobias, Theis
Ziel(e) der Sitzung? | Den Schrittmotor einbauen
1. Verlauf | Sammlung von Vorgängen, Ideen zur Programmierung
2. Ergebnisse | Serielles Protokoll implementiert
3. Weiterarbeit | Schrittmotor intrigieren

Oldenburg, den 12.02.2014 | Tobias Beyer

Lfd. Nr. : 10 | Protokoll | Bemerkungen:

Arbeitsgruppe: Gruppenthema: | Tarek, Sören, Tobias, Theis, Garrit µC über Internet
Zeit / Ort: Anwesende: | 08:56 Oldenburg (im BZTG) Tarek, Tobias, Theis
Ziel(e) der Sitzung? | An der Dokumentation weiterarbeiten, die Benennung der Protokoll-Dateien verbessern
1. Verlauf | Sammlung von Vorgängen, Ideen zur Programmierung
2. Ergebnisse | Schrittmotor weiterbau, OIL
3. Weiterarbeit | Raspberry erweitern

Oldenburg, den 17.02.2014 | Tobias Beyer

Lfd. Nr. : 11 | Protokoll | Bemerkungen:

Arbeitsgruppe: Gruppenthema: | Tarek, Sören, Tobias, Theis, Garrit µC über Internet
Zeit / Ort: Anwesende: | 08:56 Oldenburg (im BZTG) Tarek, Tobias, Theis
Ziel(e) der Sitzung? | An der Dokumentation weiterarbeiten
1. Verlauf | Sammlung von Vorgängen, Ideen zur Programmierung
2. Ergebnisse | Infrarot-Distanz-Sensor anbauen
3. Weiterarbeit | OIL aktualisieren, Programmierarbeit fortsetzen.

Oldenburg, den 19.02.2014 | Tobias Beyer

Lfd. Nr. : 12 | Protokoll | Bemerkungen:

Arbeitsgruppe: Gruppenthema: | Tarek, Sören, Tobias, Theis, Garrit µC über Internet
Zeit / Ort: Anwesende: | 08:56 Oldenburg (im BZTG) Tarek, Tobias, Theis
Ziel(e) der Sitzung? | Infrarot-Distanz-Sensor
1. Verlauf | Sammlung von Vorgängen, Ideen zur Programmierung
2. Ergebnisse | Programmierung Infrarot-Distanz-Sensor
3. Weiterarbeit | Zusammensetzung der Dokumentation

Oldenburg, den 24.02.2014 | Tobias Beyer

Lfd. Nr. : 13 | Protokoll | Bemerkungen:

Arbeitsgruppe: Gruppenthema: | Tarek, Sören, Tobias, Theis, Garrit µC über Internet
Zeit / Ort: Anwesende: | 08:56 Oldenburg (im BZTG) Tarek, Tobias, Theis
Ziel(e) der Sitzung? | An der Dokumentation weiterarbeiten
1. Verlauf | Sammlung von Vorgängen, Ideen zur Programmierung
2. Ergebnisse | Dokumentation erweitert
3. Weiterarbeit | Dokumentation erweitern

Oldenburg, den 26.02.2014 | Tobias Beyer

Lfd. Nr. : 14 | Protokoll | Bemerkungen:

Arbeitsgruppe: Gruppenthema: | Tarek, Sören, Tobias, Theis, Garrit µC über Internet
Zeit / Ort: Anwesende: | 08:56 Oldenburg (im BZTG) Tarek, Tobias, Theis
Ziel(e) der Sitzung? | An der Dokumentation weiterarbeiten
1. Verlauf | Sammlung von Vorgängen, Ideen zur Programmierung
2. Ergebnisse | Dokumentation erweitert
3. Weiterarbeit | Dokumentation erweitert, OIL , Grundlegendes

Oldenburg, den 03.03.2014 | Tobias Beyer

Lfd. Nr. : 15 | Protokoll | Bemerkungen:

Arbeitsgruppe: Gruppenthema: | Tarek, Sören, Tobias, Theis, Garrit µC über Internet
Zeit / Ort: Anwesende: | 08:56 Oldenburg (im BZTG) Tarek, Tobias, Theis
Ziel(e) der Sitzung? | An der Dokumentation weiterarbeiten, OIL, Grundlegendes
1. Verlauf | Sammlung von Vorgängen, Ideen zur Programmierung
2. Ergebnisse | Es wurde an der Dokumentation geschrieben, Software-Test
3. Weiterarbeit | Dokumentation abschließen, Allgemeine Tests und Überprüfung der Dateien

Oldenburg, den 05.03.2014 | Tobias Beyer

Lfd. Nr. : 16 | Protokoll | Bemerkungen:

Arbeitsgruppe: Gruppenthema: | Tarek, Sören, Tobias, Theis, Garrit µC über Internet
Zeit / Ort: Anwesende: | 08:56 Oldenburg (im BZTG) Tarek, Tobias, Theis
Ziel(e) der Sitzung? | An der Dokumentation fertigstellen, Allgemeine Tests
1. Verlauf | Sammlung von Vorgängen, Ideen zur Programmierung
2. Ergebnisse | Dokumentation fertigstellen, Präsentation erstellen, Abschluss-Tests
3. Weiterarbeit | Abgabe

Oldenburg, den 10.03.2014 | Tobias Beyer

Code

#!/bin/bash

# Steuerungsprogramm des Roboters

# Autor: Jan-Tarek Butt

# Datum: 12.03.2014

clear

RPI_WLAN_IPV6=fe80::9644:52ff:fe04:2db6

RPI_ETH_IPV6=fe80::ba27:ebff:fecd:5984

PORT=4444

LP_PORT=4445

W_INTERFACE=wlan0

E_INTERFACE=eth0

STATUS=0

echo "Ping test..."

ping6 -c 1 $RPI_WLAN_IPV6%$W_INTERFACE

WLANW=$?

ping6 -c 1 $RPI_WLAN_IPV6%$E_INTERFACE

WLANE=$?

ping6 -c 1 $RPI_ETH_IPV6%$E_INTERFACE

ETHE=$?

ping6 -c 1 $RPI_ETH_IPV6%$W_INTERFACE

ETHW=$?

if [ $WLANW -ne 0 -a $WLANE -ne 0 -a $ETHE -ne 0 -a $ETHW -ne 0 ]; then

echo "Roboter nicht errechtbar!"

exit

fi;

if [ $WLANW -eq 0 ]; then

INTERFACE="$RPI_WLAN_IPV6%$W_INTERFACE"

echo "Wlan verbindung"

fi;

if [ $WLANE -eq 0 ]; then

INTERFACE="$RPI_WLAN_IPV6%$E_INTERFACE"

echo "Wlan verbindung"

fi;

if [ $ETHE -eq 0 ]; then

INTERFACE="$RPI_ETH_IPV6%$E_INTERFACE"

echo "Lan verbindung"

fi;

if [ $ETHW -eq 0 ]; then

INTERFACE="$RPI_ETH_IPV6%$W_INTERFACE"

echo "Lan verbindung"

fi;

echo "Befel eingeben:"

while true

do

read -n 1 -s COMMAND

echo $COMMAND

if [ "$COMMAND" == "1" ]; then

nc -6lp 5001 | mplayer -fps 15 -cache 512 - &

sleep 1

echo "1" | nc -6 $INTERFACE $PORT

fi;

if [ "$COMMAND" == "w" ]; then

echo $COMMAND | nc -6 $INTERFACE $PORT

fi;

if [ "$COMMAND" == "s" ]; then

echo $COMMAND | nc -6 $INTERFACE $PORT

fi;

if [ "$COMMAND" == "a" ]; then

echo $COMMAND | nc -6 $INTERFACE $PORT

fi;

if [ "$COMMAND" == "d" ]; then

echo $COMMAND | nc -6 $INTERFACE $PORT

fi;

if [ "$COMMAND" == "q" ]; then

echo $COMMAND | nc -6 $INTERFACE $PORT

fi;

done

#!/bin/bash

# Raspbarry PI Server zur Steuerung des Roboters

# Autor: Jan-Tarek Butt

# Datum: 12.03.2014

clear

PORT=4444

BAUTRATE=57600

SCHNITSTELLE="/dev/ttyUSB0"

LP_ADRESSE="fe80::223:aeff:fe42:21b1%wlan0"

LP_PORT=4445

echo "Server start..."

while true

do

stty -F $SCHNITSTELLE raw ispeed $BAUTRATE ospeed $BAUTRATE cs8 -ignpar -cstopb -echo

COMMAND=$( nc -6lp $PORT )

echo $COMMAND

read -i -s Line < /dev/ttyUSB0

echo $Line

if [ "$COMMAND" == "1" ]; then

raspivid -w 640 -h 480 -t 999999 -fps 10 -b 4000000 -o - | nc -6 fe80::223:14ff:fee1:aa80%wlan0 5001 &

fi;

if [ "$COMMAND" == "s" ]; then

echo -n "1" >$SCHNITSTELLE

echo -n "2" >$SCHNITSTELLE

echo -n "3" >$SCHNITSTELLE

echo -n "255" >$SCHNITSTELLE

echo -n "255" >$SCHNITSTELLE

echo -n "1" >$SCHNITSTELLE

fi;

if [ "$COMMAND" == "w" ]; then

echo -n "1" >$SCHNITSTELLE

echo -n "1" >$SCHNITSTELLE

echo -n "4" >$SCHNITSTELLE

echo -n "255" >$SCHNITSTELLE

echo -n "255" >$SCHNITSTELLE

echo -n "1" >$SCHNITSTELLE

fi;

if [ "$COMMAND" == "d" ]; then

echo -n "1" >$SCHNITSTELLE

echo -n "2" >$SCHNITSTELLE

echo -n "3" >$SCHNITSTELLE

echo -n "255" >$SCHNITSTELLE

echo -n "000" >$SCHNITSTELLE

echo -n "1" >$SCHNITSTELLE

fi;

if [ "$COMMAND" == "a" ]; then

echo -n "1" >$SCHNITSTELLE

echo -n "2" >$SCHNITSTELLE

echo -n "3" >$SCHNITSTELLE

echo -n "000" >$SCHNITSTELLE

echo -n "255" >$SCHNITSTELLE

echo -n "1" >$SCHNITSTELLE

fi;

if [ "$COMMAND" == "q" ]; then

echo -n "1" >$SCHNITSTELLE

echo -n "5" >$SCHNITSTELLE

echo -n "5" >$SCHNITSTELLE

fi;

done

# Kamera Servo steuerung

# Autor: Jan-Tarek Butt

# Datum: 12.03.2014

import RPi.GPIO as GPIO

import time

import os

# Pin 26 als Ausgang deklarieren

GPIO.setwarnings(False)

GPIO.setmode(GPIO.BOARD)

GPIO.setup(26, GPIO.OUT)

while True:

# PWM mit 50Hz an Pin 26 starten

Servo = GPIO.PWM(26, 50)

# Richtungseingabe

Eingabe = raw_input("Bitte treffen Sie Ihre Wahl: ")

# Richtung "Rechts"

if(Eingabe == "r"):

# Schrittweite eingeben

Schritte = raw_input("Schrittweite: ")

print Schritte, "Schritte nach Rechts"

# PWM mit 10% Dutycycle (2ms) generieren

Servo.start(10)

for Counter in range(int(Schritte)):

time.sleep(0.01)

# PWM stoppen

Servo.stop()

# Mittelstellung einnehmen

elif(Eingabe == "m"):

Servo.start(7)

print "Drehung in die Mitte"

time.sleep(1)

Servo.stop()

# Richtung "Links"

elif(Eingabe == "l"):

# Schrittweite eingeben

Schritte = raw_input("Schrittweite: ")

print Schritte, "Schritte nach Links"

# PWM mit 5% Dutycycle (1ms) generieren

Servo.start(5)

for Counter in range(int(Schritte)):

time.sleep(0.01)

# PWM stoppen

Servo.stop()

# Programm beenden

elif(Eingabe == "q"):

print "Programm wird beendet......"

os._exit(1)

Servo.stop()

GPIO.cleanup()

# Ungueltige Eingabe

else:

print "Ungueltige Eingabe!"

/*

BFGTmega32.h

header-Datei für die Benutzung des µC-Boards "BFGTmega32"

des BZTG Oldenburg für das LCDisplay, die EEPROM-Nutzung,

die Nutzung der seriellen Schnittstelle, ...

am

Bildungszentrum für Technik und Gestaltung der Stadt Oldenburg

Standard: LC-Display an PORTB

*/

// Definitionen für Bitmanipulationen

#define setbit(PORT, bit) (PORT|= (1<<bit)) // Bit setzen

#define clearbit(PORT, bit) (PORT&= ~(1<<bit)) // Bit löschen

#define togglebit(PORT, bit) (PORT^= (1<<bit)) // Bit invertieren

// Definitionen für LCDisplays, die kompatibel sind zu HD44780

// Pinning adapted to set interrupt pins free

// LCD control commands

#define LCD_CLEAR 0x01 /*Clear display: 0b 0000 0001 */

#define LCD_HOME 0x02 /*Cursor home: 0b 0000 0010 */

#define LCD_ON 0x0C /*Cursor invisible: 0b 0000 1100 */

#define LCD_OFF 0x08 /*Display off: 0b 0000 1000 */

#define POS_01 0x80 /*Zeile 1 - Spalte 0 0b 1000 0000 */

#define POS_02 0xC0 /*Zeile 2 - Spalte 0 0b 1100 0000 */

// Festlegung der PORT-Pins

#define LCDPORT PORTB

#define LCDDDR DDRB

#define LCD_PIN_RS 2

#define LCD_PIN_E 3

#define LCD_PIN_D4 4

#define LCD_PIN_D5 5

#define LCD_PIN_D6 6

#define LCD_PIN_D7 7

#define COMMAND 0

#define DATA 1

void toggle_enable_pin(void) // Unterstützungsfunktion zum Invertieren von Bits

{

setbit(LCDPORT, LCD_PIN_E);

clearbit(LCDPORT, LCD_PIN_E);

}

#ifdef _UTIL_DELAY_H_ // wenn delay.h eingebunden ist dann ...

void lcd_send(unsigned char type, unsigned char c) // wird von lcd_write() aufgerufen

{

unsigned char sic_c; // backup for c

// send high nibble

sic_c = c; // save original c

sic_c &= ~0x0f; // set bit 0-3 == 0

if (type==DATA) sic_c |= (1<<LCD_PIN_RS); // data: RS = 1

LCDPORT = sic_c; toggle_enable_pin(); // send high nibble

// send low nibble

sic_c = c; // save original c

sic_c = sic_c<<4; // exchange nibbles

sic_c &= ~0x0f; // set bit 0-3 == 0

if (type==DATA) sic_c |= (1<<LCD_PIN_RS); // data: RS = 1

LCDPORT = sic_c; toggle_enable_pin(); // send low nibble

_delay_ms(5); // Wait for LCD controller

}

void lcd_init() // Initializing des LCDisplays - vgl. Datenblatt

{

/* Set Port to Output */

LCDDDR = 0xFF;LCDPORT = 0x00;

_delay_ms(50); // Wait for LCD

/* 4-bit Modus config */

setbit(LCDPORT, LCD_PIN_D5); // Funktion Set : 4-Bit-Modus

_delay_ms(5);

/* 2 Lines, 4-Bit Mode */

lcd_send(COMMAND, 0x28); // Funktion Set : 2zeilige Display, 5x7 dots

lcd_send(COMMAND, LCD_OFF); lcd_send(COMMAND, LCD_CLEAR);

lcd_send(COMMAND, 0x06); // Entry Mode Set : Inkrement, Cursor schieben

lcd_send(COMMAND, LCD_ON);

}

void lcd_write(char *data) // Schreibt eine Zeichenkette (String) auf das Display

{

while(*data){lcd_send(DATA, *data); data++;}

}

void lcd_set_cursor(uint8_t zeile, uint8_t zeichen)

// Cursor auf Zeile und Zeichen setzen

{

uint8_t i;

switch (zeile)

{

case 1: i=0x80+0x00+zeichen; break; // 1. Zeile

case 2: i=0x80+0x40+zeichen; break; // 2. Zeile

default: return; // invalid line

}

lcd_send(COMMAND, i);

}

#endif

void eepromwritebyte(uint16_t adresse, uint8_t data) // Byte in EEPROM schreiben

{

while(EECR & (1<<EEWE));

EEAR = adresse;

EEDR = data;

EECR |= (1<<EEMWE);

EECR |= (1<<EEWE);

}

uint8_t eepromreadbyte(uint16_t adresse) // Byte aus EEPROM lesen

{

while(EECR & (1<<EEWE));

EEAR = adresse;

EECR |= (1<<EERE);

return EEDR;

}

#ifdef BAUDRATE // Wenn BAUDRATE definirt ist dann ...

void uart_init(void) // Initialisierung der seriellen Schnittstelle

{

UBRRL = (unsigned char)(F_CPU/(BAUDRATE*16L)-1);

// Formel zur Berechnung der Baudrate variabel zur Tacktferqenz

UCSRB |= (1<<TXEN) | (1<<RXEN) | (1<<RXCIE);

// Sendemodul aktivieren, Empfangsmodul aktivieren, // Char Interuppt Aktivieren

UCSRC |= (1<<UCSZ1) | (1<<UCSZ0) | (1<<URSEL);

// Länge eines Zeichens auf 8 bit setzen

// URSEL benötigt um auf UCSRC zuzugreifen

}

void uart_send_char(unsigned char c) // Sendet einen einzelnen char

{

while (!(UCSRA & (1<<UDRE))); // Warten bis der UART zum Senden bereit

UDR = c; // c in Ausgangsregister schreiben

// Übertragung wird automatisch gestartet

}

void uart_send_string(char *s) // Senset einen String auf die serielle Schnittstelle

{

while(*s) //solange s != \0

{

uart_send_char(*s); //einzelnes Zeichen senden

s++; //weiter zum nächsten Zeichen

}

}

int uart_get_int(void) // Empfängt ein integer

{

while(bit_is_clear(UCSRA,RXC)); //warten auf Receive Complete

return UDR;

}

void uart_send_int(unsigned int zahl, int sges)

// Sendet einen integer der Zeichenlänge sges

{

//Ausgabe der Integerzahl zahl formatiert mit sges Stellen

char buffer[17];

uint8_t l=0,n;

char *z=buffer;

utoa(zahl,buffer,10);

while(*z!=0){l++; z++;} //Bufferlänge l

for(n=l;n<sges;n++) uart_send_char(' ');

uart_send_string(buffer);

}

void uart_send_float(float zahl, int sges, int snach)

// Sendet einen float mit sges Zeichen und snach Nachkommastellen

{

//Ausgabe einer Fließkommazahl mit sges Gesamtstellen.

//Hiervon sind snach Nachkommastellen.

//Die Nachkollastellen werden gerundet.

char buffer[16];

dtostrf(zahl,sges,snach,buffer);

uart_send_string(buffer);

}

int ausgabe(void) // Beispiel einer Ausgabe und Tastaturabfrage

{

int z;

uart_send_string("\n\n\r"); // 2x Zeilenumbruch, 1x Rücklauf nach links

uart_send_string("1) Digitale Ausgaben an den Ports B und C\n\r");

uart_send_string("2) Taster als digitale Eingänge an Port A\n\r");

uart_send_string("\nGeben Sie Ihre Wahl ein: ");

z=uart_get_int();

z=z-48;

return z;

}

#endif

/*

* ATmega32 Steuerungs Programm

*

* Created: 15.01.2014 14:23:42

* Author: Jan-Tarek Butt

DDRA =||PA1|PA2|PA3|||||

DDRB =|PB0||PB2||PB4||PB6||

DDRC =|PC0|PC1|PC2|PC3|PC4|PC5|PC6|PC7|

DDRD =|PD0|PD1|PD2||PD4|PD5|PD6||

DC_Motor =PC2,PC3,PC4,PC5

Serial =PD0,PD1

externe Interrups =PD2

PWM =PD4,PD5

IR_Sensor =PA1,PA2,PA3

Ultraschall =PC0,PC7

Polulu =PB0,PB2,PB4,PB6

Serial Übertragung =PC6

uC_aktiv =PC1

Lichtschranke =PD6

Schrittmotor =PB0,PB2,PB4,PB6

*/

#define F_CPU 16000000 // Taktfrequenz fest legen

#define BAUDRATE 57200

// Baudrate fuer die serielle Schnittstelle fest legen

#include <avr/io.h>

#include <avr/sleep.h> // lib for Sleep mode

#include <avr/interrupt.h> // lib for Interrupts

#include <util/delay.h> // lib for delays

#include "BFGTmega32.h" // lib for Serial communication

int I_Wert; // ISR variable fuer serielle Kommunikation starten

int rPI; // ISR variable pruefen ob raspberry PI erreichbar ist

int unsigned zaehler= 0;

// ISR Timer0 variable fuer overflow benoetigt fuer Ultraschall Radar

ISR(INT0_vect) // Interrupt service routine loest aus wenn Raspberry errechtbar ist.

{

cli(); // Deaktivieren aller Interrupts

if (PIND & (1<<PD2)) // Wenn PD2 == High dann ...

{

rPI = 1; // rPI == Online

}else

{

rPI = 0; // rPI == Offline

}

sei(); // Aktivieren aller Interrupts

}

ISR(USART_RXC_vect)

// Interrupt Service Routine loest aus wenn Daten empfangen werden

{

cli(); // Deaktivieren aller Interrupts

while(bit_is_clear(UCSRA,RXC)); // warten auf Receive Complete

I_Wert = UDR;

sei(); // Aktivieren aller Interrupts

}

ISR (TIMER0_OVF_vect)

// Interrupt Service Routine loest aus wenn timer0 Register ueberlaeuft

{

cli(); // Deaktivieren aller Interrupts

zaehler++;

sei(); // Aktivieren aller Interrupts

}

void Motor_richtung(int Motor_R, int Motor_L) // Motor richtungs Steuerung

{

if (Motor_R == 1) // Rechter Motor

{

PORTC &= ~(1<<PC3);

PORTC |= (1<<PC2);

}

if (Motor_R == 2)

{

PORTC &= ~(1<<PC2);

PORTC |= (1<<PC3);

}

if (Motor_L == 3) // Linker Motor

{

PORTC &= ~(1<<PC5);

PORTC |= (1<<PC4);

}

if (Motor_L == 4)

{

PORTC &= ~(1<<PC4);

PORTC |= (1<<PC5);

}

if (Motor_R == 5 || Motor_L == 5) // Motoren Ausschalten

{

PORTC &= ~((1<<PC2)|(1<<PC3)|(1<<PC4)|(1<<PC5));

}

}

int SensorFront(void) // Messung Abstand Front

{

ADMUX |= (1 << MUX1); // PA2 fuer AD Wandlung EIN

ADCSRA |= (1 << ADSC); // AD-Wandlung starten

_delay_us(500);

int IR[4] = {0,ADCW,0,0}; // AD-Wandlung 10-Bit

ADCSRA |= (1 << ADSC); // AD-Wandlung starten

_delay_us(500);

IR[2] = ADCW; // AD-Wandlung 10-Bit

ADCSRA |= (1 << ADSC); // AD-Wandlung starten

_delay_us(500);

IR[3] = ADCW; // AD-Wandlung 10-Bit

IR[0] = ((IR[1]+IR[2]+IR[3])/3); // Mittlung der AD-Wandlung

ADMUX &= ~(1 << MUX1); // PC2 fuer AD Wandlung AUS

double d = ((1 - ((IR[0] * 0.0048828125) * (1.0 / 18.0))) / ((IR[0] * 0.0048828125) * (2.0 / 27.0)))*2; // Distanz Umrechnung in cm

if (d < 5) // Wenn d kleiner als 5 dann ...

d = 400; // Minimum 5cm, Meldung 400

else if (d > 50) // Wenn d größer als 50 dann ...

d = 300; // Maximum 50cm, Meldung 300

return d; // Rückgabe d

}

int SensorRechts(void) // Messung Abstand Rechts

{

ADMUX |= ((1 << MUX0)|(1 << MUX1)); // PA3 für AD Wandlung EIN

ADCSRA |= (1 << ADSC); // AD-Wandlung starten

_delay_us(500);

int IR[4] = {0,ADCW,0,0}; // AD-Wandlung 10-Bit

ADCSRA |= (1 << ADSC); // AD-Wandlung starten

_delay_us(500);

IR[2] = ADCW; // AD-Wandlung 10-Bit

ADCSRA |= (1 << ADSC); // AD-Wandlung starten

_delay_us(500);

IR[3] = ADCW; // AD-Wandlung 10-Bit

IR[0] = ((IR[1]+IR[2]+IR[3])/3); // Mittlung der AD-Wandlung

ADMUX &= ~((1 << MUX0)|(1 << MUX1)); // PC3 für AD Wandlung AUS

double d = ((1 - ((IR[0] * 0.0048828125) * (1.0 / 18.0))) / ((IR[0] * 0.0048828125) * (2.0 / 14.0)))*2; // Distanz Umrechnung in cm

if (d < 5) // Wenn d kleiner als 5 dann ...

d = 400; // Minimum 5cm, Meldung 400

else if (d > 50) // Wenn d größer als 50 dann ...

d = 300; // Maximum 50cm, Meldung 300

return d; // Rückgabe d

}

int SensorLinks(void) // Messung Abstand Links

{

ADMUX |= (1 << MUX0); // PA1 für AD Wandlung EIN

ADCSRA |= (1 << ADSC); // AD-Wandlung starten

_delay_us(500);

int IR[4] = {0,ADCW,0,0}; // AD-Wandlung 10-Bit

ADCSRA |= (1 << ADSC); // AD-Wandlung starten

_delay_us(500);

IR[2] = ADCW; // AD-Wandlung 10-Bit

ADCSRA |= (1 << ADSC); // AD-Wandlung starten

_delay_us(500);

IR[3] = ADCW; // AD-Wandlung 10-Bit

IR[0] = ((IR[1]+IR[2]+IR[3])/3); // Mittlung der AD-Wandlung

ADMUX &= ~(1 << MUX0); // PC4 für AD Wandlung AUS

double d = ((1 - ((IR[0] * 0.0048828125) * (1.0 / 18.0))) / ((IR[0] * 0.0048828125) * (2.0 / 12.0)))*2; // Distanz Umrechnung in cm

if (d < 5) // Wenn d kleiner als 5 dann ...

d = 400; // Minimum 5cm, Meldung 400

else if (d > 50) // Wenn d größer als 50 dann ...

d = 300; // Maximum 50cm, Meldung 300

return d; // Rückgabe d

}

int Usensor(void) // Messung Ultraschall Sensor

{

PORTC |= (1<<PC0);

_delay_us(10);

PORTC &= ~(1<<PC0); // Ultraschall Trigger ausloesen

while((PINC&(1<<PC7))==0); // Wartet auf Steigende Flanke

TCCR0 |= (1<<CS01); // Timer0 mit Prescale von 8 starten

while(PINC&(1<<PC7)); // Warten solange Echo High

TCCR0 = 0; // Timer0 Stoppen

double t = (((zaehler<<8)+TCNT0)/2)*0.5; // zeit in us umrechnen

unsigned int s = (0.0343*t); // Distanz in cm berechnen

zaehler=0; // Timer 0 Overflow auf Null setzen

uart_send_string(" UL:");

uart_send_int(s,1);

uart_send_string(" "); // Serielle ausgaben von Ultraschall werten

_delay_ms(1);

return 0;

}

int SchrittMotor(void) // Schrittmotor Steuerung fuer Ultraschall Radar

{

PORTB &= ~(1<<PB0); // Schrittmotor Endstufe ENABLE

PORTB |= (1<<PB4);

_delay_ms(5);

PORTB &= ~(1<<PB4);

_delay_ms(5); // Ein step vorwaerst

PORTB |= (1<<PB0); // Schrittmotor Endstufe DIESABLE

int Smotor = 0;

if (PIND & (1<<PD6)) // Wenn Lichtschranke ausloest dann ...

{

Smotor = 1;

}

Usensor(); // Ultraschall Messung Ausloesen

return Smotor;

}

int Sensor_Ausgabe(void) //Ausgabe der Sensoren

{

int Sensoren[4]={SensorFront(),SensorRechts(),SensorLinks(),SchrittMotor()};

// Array, Sensoren auslesen

uart_send_string("SF:");

uart_send_int(Sensoren[0],1); // Infrarot Front Sensor ausgeben

uart_send_string(" SR:");

uart_send_int(Sensoren[1],1); // Infrarot Rechter Sensor ausgeben

uart_send_string(" SL:");

uart_send_int(Sensoren[2],1); // Infrarot Linker Sensor ausgeben

uart_send_string(" SM:");

uart_send_int(Sensoren[3],1);

// Schrittmotor Referenz Signal der Lichtschranke ausgeben

uart_send_string("\n\r"); // Zeilenumbruch

_delay_ms(1);

return 0;

}

int main(void)

{

uart_init(); // Serial Inizialisirung

DDRC = 0b01111111;

DDRB = 0b11111111;

DDRA = 0b11110001;

DDRD &= ~((1 << PD2)|(1<<PD6)); // INT0 und Lichtschranke input...

DDRD |= (1<<PD4)|(1<<PD5); // PWM Ausgaenge festlegen

ADCSRA = 0b10000111; // Prescaler 128

ADMUX |= (1<<REFS0); // 5V Referenz Spannung

TCCR1A |= (1<<WGM10)|(1<<COM1A1)|(1<<COM1B1);

TCCR1B |= (1<<WGM12)|(1<<CS12); // Prescaler 256

GICR |= (1<<INT0); // IRS INT0 externer Interrupt aktivieren

MCUCR |= (1<<ISC00); // ISR INT0 Reaktion auf jede aenderung

PORTB |= ((1<<PB0)|(1<<PB6)); // Schrittmotor Endstufe aus schalten

TIMSK |= (1<<TOIE0); // Timer0 Overflow Interrupt erlauben

while(1)

{

sei(); // Aktivieren aller Interrupts

uart_init(); // Serial Inizialisirung

if (rPI == 1) // Wenn INT0 == High dann ...

{

PORTC |= (1<<PC1);

Sensor_Ausgabe(); // Pereperie auswerten

if (I_Wert == 49) // Wenn Eingabe == 49 dann ...

{

cli(); // Deaktivieren aller Interrupts

I_Wert = 0;

PORTC |= (1<<PC6);

// anzeigen das Daten jetzt uebertragen werden koennen

int Motor_R = (uart_get_int()-48);

// Richtungs Vorgabe der Motoren 1-2 Vor-Rueckwaerts 5 = Motoren Aus

int Motor_L = (uart_get_int()-48);

// Richtungs Vorgabe der Motoren 3-4 Vor-Rueckwaerts 5 = Motoren Aus

if(Motor_R > 5 || Motor_L > 5)

// Wenn Eingabe größer als 5 dann ...

{

PORTC &= ~(1<<PC6);

// anzeigen das Daten nicht mehr uebertragen werden koennen

return main();

// Zurueck an denn Anfang der main Funktion

}

if(Motor_R == 5 || Motor_L == 5)

// Wenn Eingabe == 5 dann ...

{

Motor_richtung(Motor_R,Motor_L);

// uebergabe an Motor_richtung

PORTC &= ~(1<<PC6);

// anzeigen das Daten nicht mehr uebertragen werden koennen

return main();

// Zurueck an denn Anfang der main Funktion

}

int PWM[4] = {0,(uart_get_int()-48),(uart_get_int()-48),(uart_get_int()-48)}; // Annahmen der Motor Geschwindigkeit 0-255

PWM[0] = (PWM[1]*100+PWM[2]*10+PWM[3]);

int PWM1[4] = {0,(uart_get_int()-48),(uart_get_int()-48),(uart_get_int()-48)}; // Annahmen der Motor Geschwindigkeit 0-255

PWM1[0] = (PWM1[1]*100+PWM1[2]*10+PWM1[3]);

if (PWM[0] <= 255 && PWM1[0] <= 255)

// Wenn PWM kleiner als 255 dann ...

{

uart_send_string("MR: ");

uart_send_int(Motor_R,1);

uart_send_string(" ");

uart_send_int(PWM[0],1);

uart_send_string("\n\r"); // Sende Zeilenumbruch

uart_send_string("ML: ");

uart_send_int(Motor_L,1);

uart_send_string(" ");

uart_send_int(PWM1[0],1);

uart_send_string("\n\r"); // Sende Zeilenumbruch

if ((uart_get_int()-48) == 1)

// Bestaetigung der uebertragenen werte wenn Eingabe == 1 dann ...

{

Motor_richtung(Motor_R,Motor_L);

OCR1B = PWM[0]; // PWM setzen

OCR1A = PWM1[0]; // PWM setzen

}

}

PORTC &= ~(1<<PC6);

// anzeigen das Daten nicht mehr uebertragen werden koennen

}else

{

PORTC &= ~(1<<PC6);

// anzeigen das Daten nicht mehr uebertragen werden koennen

}

}

else

{

PORTC &= ~(1<<PC1);

Motor_richtung(5,5); // uebergabe an Motor_richtung

set_sleep_mode(SLEEP_MODE_IDLE); // sleep mode Aktivieren

sleep_mode(); // uC geht Ideln

}

}

}

Zusätzliches Material:

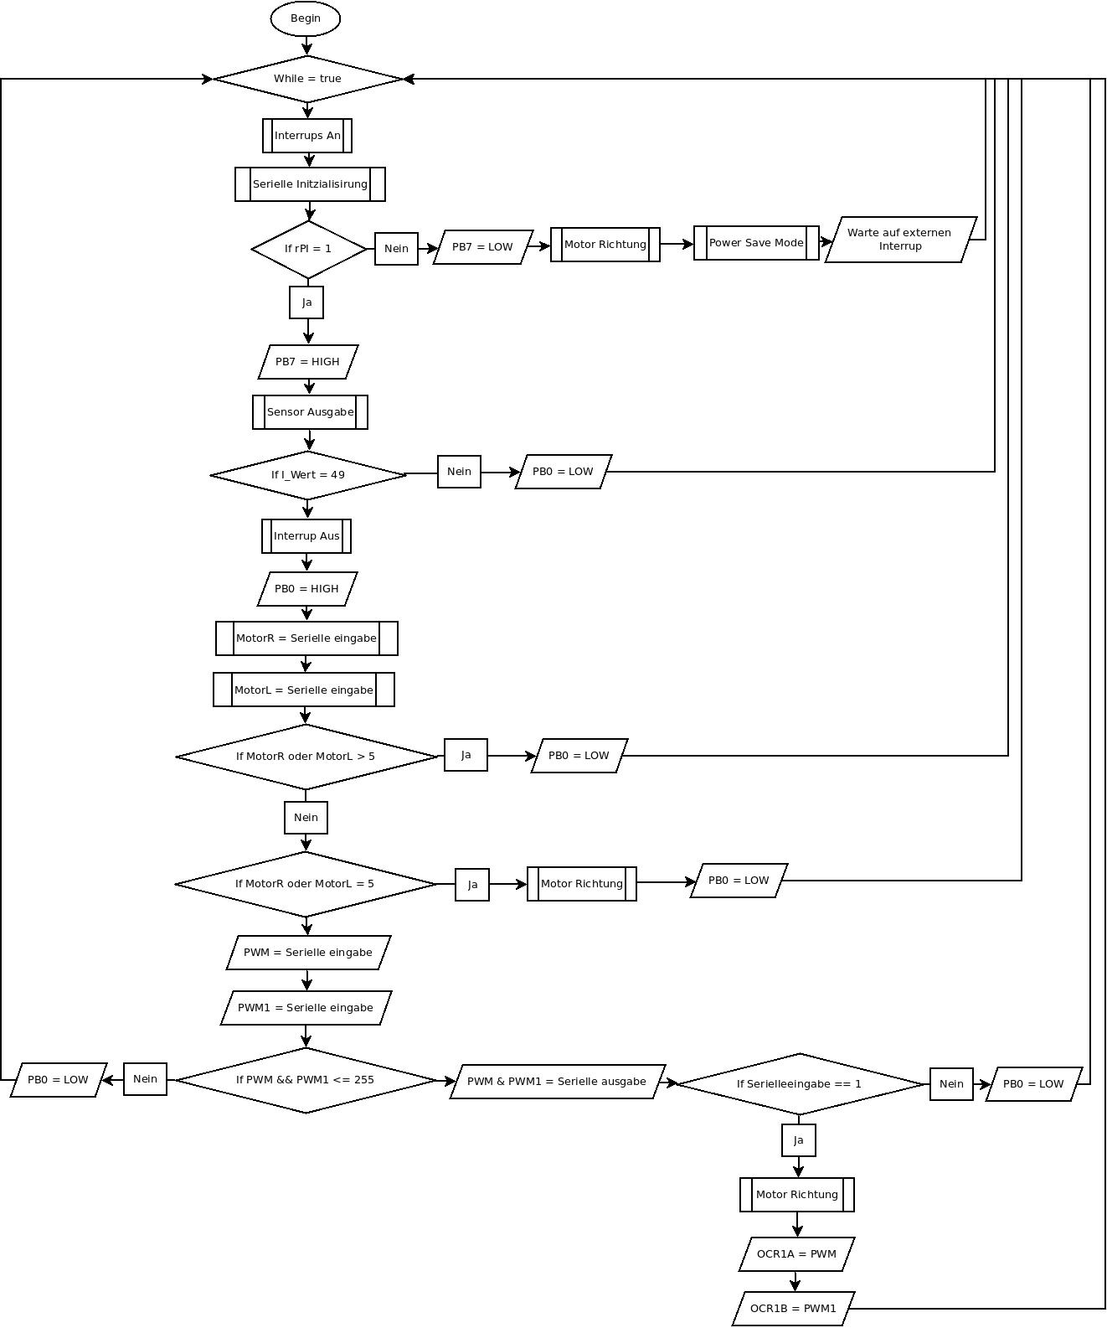
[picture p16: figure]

Flussdiagramm(Anhang 1)

Todo-liste:(Anhang 2)

Stepp 1 Mikrocontroler

Was soll der Mikrocontroler können?

- I/O Steuerung

- ADW Steuerung

- PWM Steuerung

-I2C Steuerung

Stepp 2 Microcontroler > Rassberry Pi

Wie soll der Microcontroler gesteuert werden?

- GPI/O Pins

- Serielle Steuerung

- I2C Steuerung

- JTAG Steuerung

Stepp 3 Rasberry Pi steuerung

Was soll der Rasberry können?

- Remoute Schnittstelle spielen

- Server spielen

- Protokoll Sockel bilden

- Viertual Serial Com emulirung

- SFTP Server

- Netcat

- SSH

- TCP-/IP-Stack

- ?

Stepp 4 Rasberry Pi remoute Steuerung

Wie soll der Rasberry gesteuert werden Windows/Linux?

- C# Programm (Windows)

- Webinterface (OS unabhängig)

- C Programm (Linux)

- Java Programm (Windows und Linux)

- (Video Stream Implementierung ins Programm)

Vorgangs-liste:(Anhang 3)

Nr. | Vorgang | Dauer (Tage) | Vorgänger
1 | Teamleiter wählen✔ | 1 | -
2 | Informationen sammeln✔ | 1 | 1
3 | Dokumentation starten✔ | M | 1
4 | Mikrocontroller programmieren✔ | 8 | 3
5 | Verbindung mit Mikrocontroller und Raspberry Pi programmieren✔ | 5 | 3
6 | Raspberrysteuerung programmieren✔ | 10 | 5
7 | RPI Remotesteuerung (C#) (optional) | 13 | 6
8 | Infrarotdistanzsensoren auswerten (optional)✔ | 4 | 7
9 | Ansteuerung Servomotor über GPIO (optional)✔ | 3 | 7
10 | Realisierung von visueller Übertragung (optional)✔ | 7 | 7
11 | Ultraschallradar (optional)✔ | 15 | 10
12 | Sprachausgabe des Roboters (optional) | 10 | 10
13 | Alles ausführlich testen✔ | 2 | 4-12
14 | Hardware zusammenbauen (Endzustand)✔ | 1 | 13
15 | Präsentation erstellen✔ | 1 | 14
16 | Dokumentation fertigstellen✔ | 3 | 15

Projektstrukturplan:(Anhang 4)


Dokumentation Mikrocontroller über Ethernet

Projektkurs: microcontroller über ethernet Theis Ammermann, Jan-tarek butt. sören j,tobias b 1

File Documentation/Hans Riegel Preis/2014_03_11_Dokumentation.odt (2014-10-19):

Bildungszentrum für Technik und


Gestaltung Oldenburg (BZTG)

Straßburger Str. 2

26123 Oldenburg

Tel.: 0441-98377-0

Facharbeit

Netzwerk gesteuerter Roboter

Verfasser: Jan-Tarek Butt

Betreuungslehrer: StR Rainer Lüllmann

Inhaltsverzeichnis

Einleitung......................................................................................................................Seite 2

Projektdurchführung......................................................................................................Seite 3

- Beschreibung der Konstruktion.....................................................................Seite 3-4
- Fotos, Zeichnungen, Baupläne, etc................................................................Seite 4-6
- Infrarot-Distanzsensoren................................................................................Seite 7-9
- Ultraschall Sensor............................................................................................Seite 10
- Protokoll Entwicklung.....................................................................................Seite 11
- Monolithischer Aufbau der Software Ebenen.................................................Seite 12
- Portbelegung des ATmega32's.........................................................................Seite 12

Diskussion...................................................................................................................Seite 13

- Beschreibung aufgetretener Probleme.............................................................Seite 13

Reflexion.....................................................................................................................Seite 14

- Zukünftige Projekte...............................................................................................Seite 14
- Erweiterungsmöglichkeiten...................................................................................Seite 14

Literaturverzeichnis.....................................................................................................Seite 15

Anhang....................................................................................................................ab Seite 16

Einleitung

Das Ziel der Facharbeit war es, den Mikrocontroller „BFGTmega32“ des BZTG's über WLAN/UMTS anzusteuern. Um das sichtbar zu machen, wurde der Mikrocontroller mit Rädern und Sensoren ausgestattet, sodass man ihn über das Internet als eine Art ferngesteuerten Roboter ansteuern kann. Der Roboter soll vorwärts, rückwärts, nach links und nach rechts fahren können. Der Mikrocontroller wird mit einem Raspberry PI ausgestattet. Dieser bildet die Schnittstelle zur Ansteuerung über das Internet oder über das lokale Netzwerk. Der Raspberry PI ist mit einen Debian Wheezy Linux ausgestattet. Als Software wurde mit „AVR STUDIO 6.1“ zur „C“ Programmierung des ATmega32 Mikrocontrollers gearbeitet. Des Weiteren wurden auf dem Raspberry PI die Programmiersprache „Python“ und die Script-Sprache „Bash“ verwendet. Das Steuerungsprogramm wurde ebenfalls in Bash geschrieben. Um eine Übersicht über die C Programmierung des AT-Mega32 Mikrocontroller Boards zu behalten wurde ein Flussdiagramm (siehe: Anhang) mit DIA erstellt. Um eine Steuerung über das UMTS Netz zu realisieren wird ein vServer im Internet benötigt. Dieser vServer muss eine VPN (Virtual Private Network) Verbindung zum Raspberry PI und zum Steuerungsrechner aufbauen. Wenn der Roboter nur im lokalen WLAN gesteuert werden soll genügt ein AD-Hoc Netzwerk.


Abbildung 1 Vollständiger Roboter

Durchführung des Projektes

Zu Beginn des Projektes wurde eine ToDo-Liste (siehe: Anhang) erstellt. Im Anschluss wurde eine darauf basierende Vorgangsliste (siehe: Anhang) geschrieben, die in einzelnen Etappen abgearbeitet wurde. Außerdem wurde die Vorgangsliste auf einen Projektstrukturplan (siehe: Anhang) übertragen, in welchem die Vorgänge in Kategorien eingeteilt wurden. Für dieses Projekt gibt es grundlegende Voraussetzungen, wie insbesondere die C-Programmierung und der allgemeine Umgang mit Mikrocontrollern. Das Ziel des Projektes ist es, den Mikrocontroller „ATmega32“ in Form eines Roboters mit einigen Sensoren sowie mit der Hilfe eines Raspberry PI über WLAN/UMTS anzusteuern. Von der Schule wurde ein Mikrocontroller Board und verschiedene Sensoren zur Verfügung gestellt. Der Mikrocontroller wurde nach und nach mit neuen Bauteilen versehen.

Beschreibung der Konstruktion

Angefangen wurde mit dem Raspberry PI, der den Kontakt vom Mikrocontroller zum Internet überhaupt erst möglich macht. An den ersten USB-Port wurde eine WLAN-Karte angebracht, der zweite USB-Port wurde für den USB-Seriell Adapter benötigt. Außerdem wurde eine Infrarot-Kamera zur Bildübertragung per Flachbandkabel angeschlossen; diese bietet eine visuelle Übertragungsmöglichkeit. Durch den nicht vorhandenen Infrarotfilter kann man die Kamera sowohl in einer hellen als auch in einer dunklen Umgebung nutzen. Die IR-Kamera wurde auf einem digitalen Servomotor befestigt der über die GPIO Pins des Raspberry gesteuert wird. Als dies abgeschlossen war, wurden Infrarot-Sensoren links, rechts und an der Hinterseite des Fahrzeugs angebracht. Auf dem Roboter befindet sich auch noch ein Schrittmotor der über einen Polulu Schrittmotortreiber auf der Unterseite des Roboters vom Mikrocontroller gesteuert wird. Seitwärts am Schrittmotor ist eine Lichtschranke angebracht, diese liefert ein Referenzsignal was zur Kalibrierung des Ultraschallradars notwendig ist. Auf dem Schrittmotor ist ein HC-SR04 Ultraschallsensor angebracht. Dieser erkennt in einem Umkreis von ca. 5 Metern Hindernisse. Der Mikrocontroller wird mit einem seriellen Interface über den Raspberry PI gesteuert. Auf den Raspberry PI wird mit einem nativen TCP/IP Socket gearbeitet. Über das TCP Protokoll erhält der Roboter seine Befehle und sendet seinen Status und sämtliche Sensorwerte an den Steuerungsrechner. Die Verbindung zum Raspberry PI wird über IPv6 realisiert. Um manuell auf dem Raspberry PI zu arbeiten kann man sich über SSH (Secure Shell) anmelden.

Fotos, Zeichnungen, Baupläne, etc.

Mikrocontroller

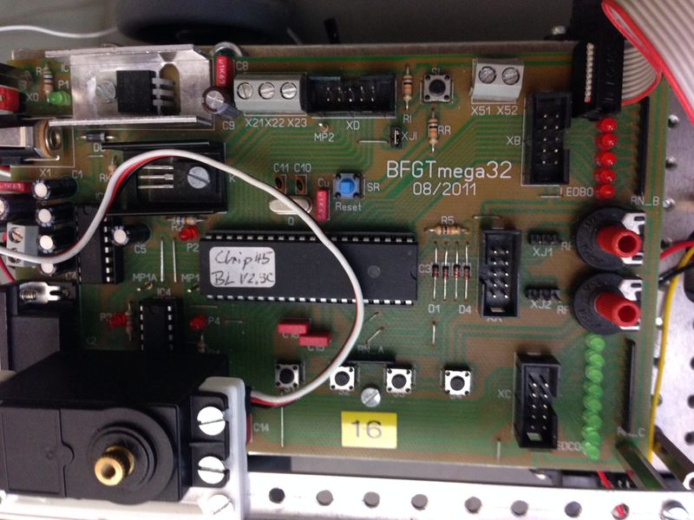
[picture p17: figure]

Abbildung 2: Mikrocontroller "BFGTmega32"

Servomotor

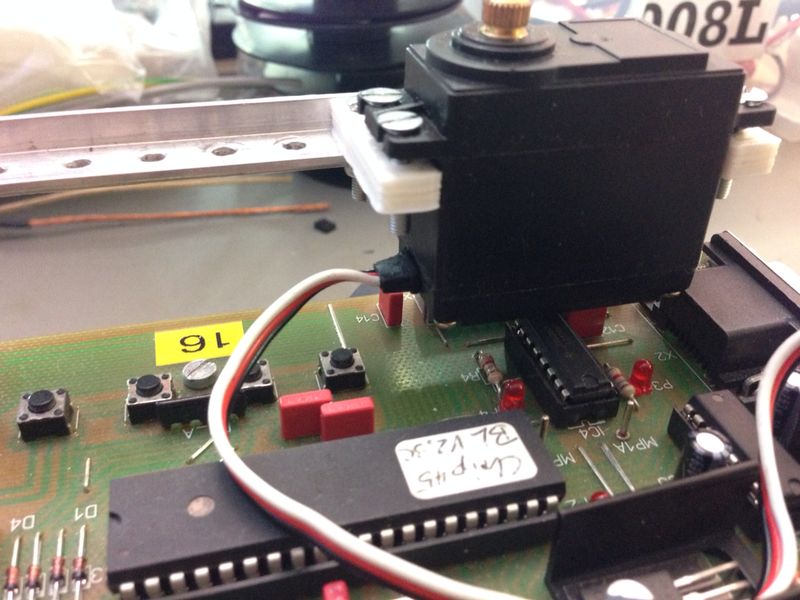
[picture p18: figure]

Abbildung 3: Servo mit 3D gedruckter Halterung

Spannungsversorgung für Roboter Komponenten

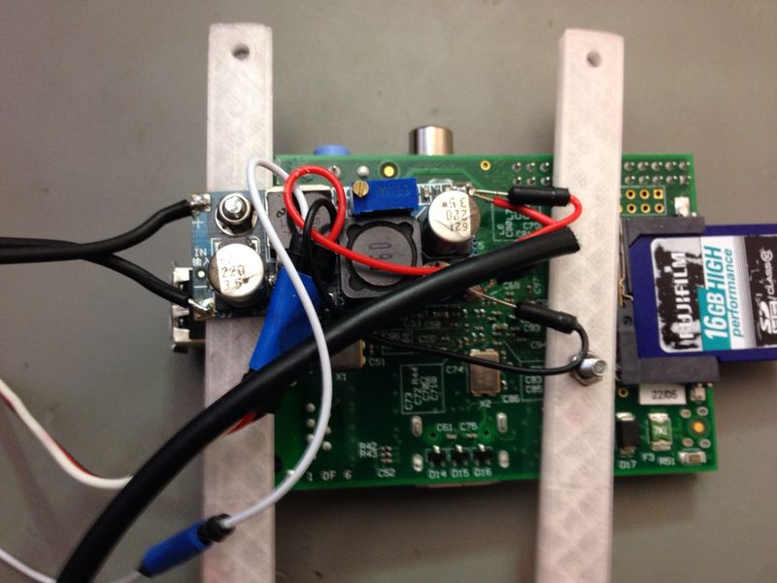
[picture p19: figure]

Abbildung 4: 5V Schaltregler für Raspberry PI und Servo

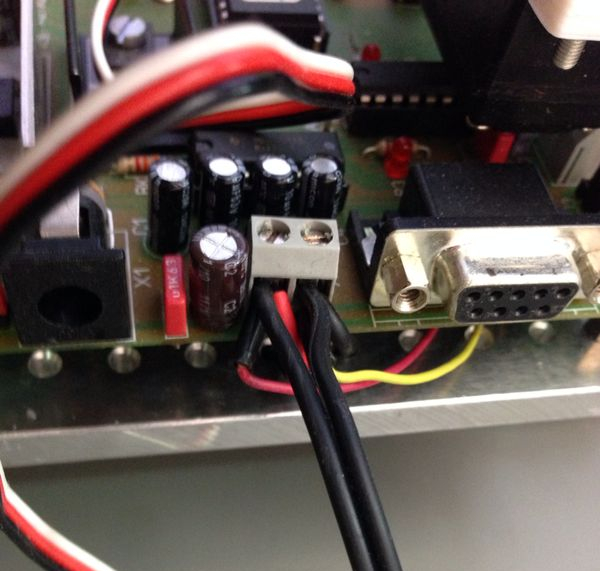
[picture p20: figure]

Abbildung 5: Spannungsversorgung des Roboters (7-12V)

GPIO Pins des Raspberry PI

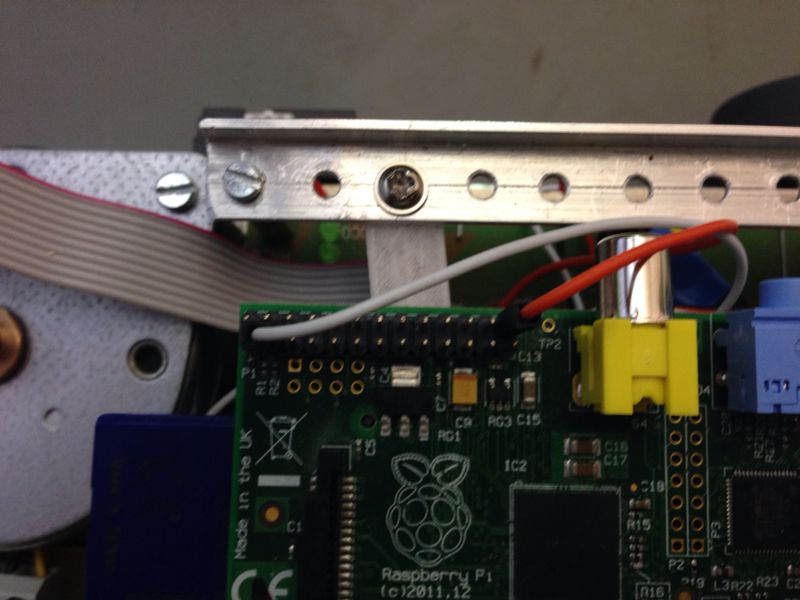
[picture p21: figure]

Abbildung 6: (Orangenes Kabel ist für ein PWM Signal des Servomotors)(Weißes Kabel ist für einen Interrupt Pin am ATmega32)

Schrittmotor Treiber

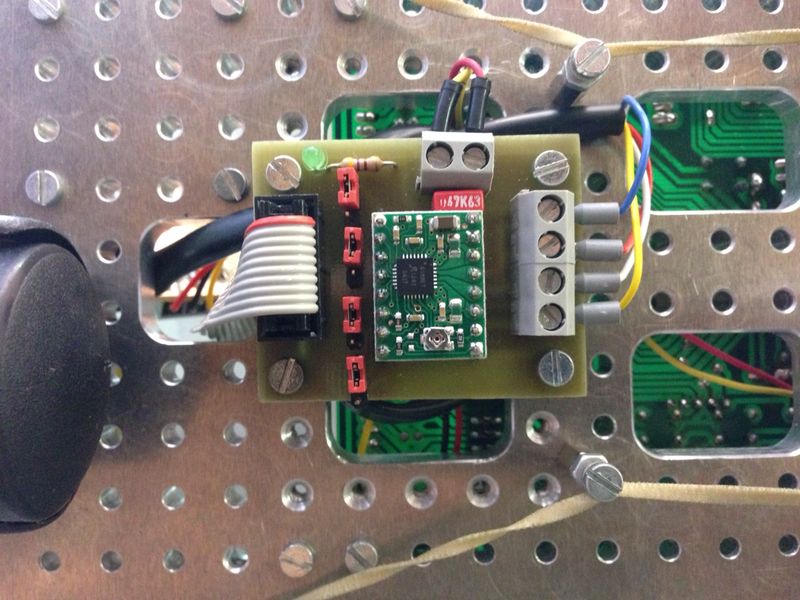
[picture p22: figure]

Abbildung 7: Polulu Schrittmotortreiber für das Ultraschall Radar

Testlauf der Roboter Komponenten

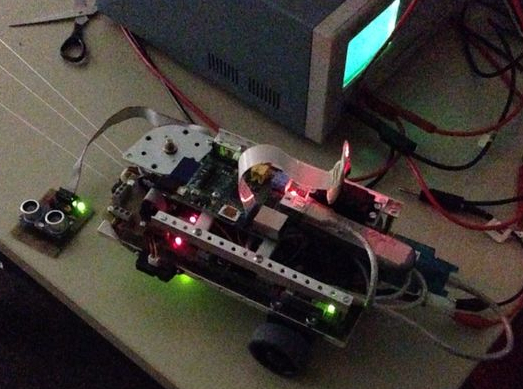
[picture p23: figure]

Abbildung 8: Prüfung ob alle Komponenten Ordnungsgemäß angeschlossen sind

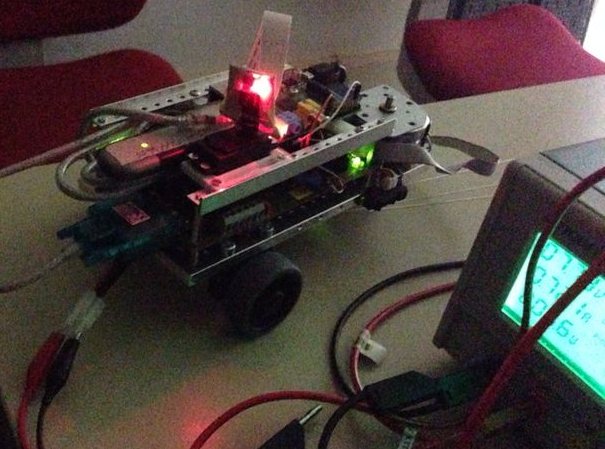
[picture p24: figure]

Abbildung 9: Prüfung der Kamerastream Übertragung

Infrarotsensoren

Im Folgenden kommen einige Berechnungen zur Funktions-Annäherung und Filterung der Infrarot-Distanzsensoren:


Kennlinie der Sharp Infrarot Sensoren


Ultraschall Sensor


Der Ultraschallsensor hat einen ungefähren Öffnungswinkel von 30°. Die Bauform ist dem oberen Bild zu entnehmen.


Die Ansteuerung des Ultraschall Sensors ist relativ komplex. Man muss ein circa 10 µs Sekunden langes Signal auf den Trigger-Pin legen und bekommt ein Echosignal auf dem Echo-Pin zurück. Die Länge des Echosignals wird mit einem Timer gemessen, da die Länge mit der gemessenen Distanz des Sensors variiert.

Protokoll Entwicklung

Entwicklung des Protokolls zwischen Raspberry PI und ATmega32:


Um eine Datenübertragung zu starten wird eine 50-49 (ASCII-Zeichen == 1) gesendet. Anschließend wartet der ATmega32 auf zwei Zeichen zwischen 1-5 für den Motorenzustand. Daraufhin sendet man zwei mal einen Wert zwischen 0-255 für das PWM, was die Geschwindigkeit der Motoren regelt. Sobald man die PWM Werte gesetzt hat, sendet der Mikrocontroller die Werte zurück: wenn die Werte äquivalent zu den eingegebenen Werten sind, wird eine 1 gesendet, was vergleichbar mit einem ACK-Byte ist. Daraufhin führt der ATmega32 seinen Befehl aus.

Monolithischer Aufbau der Software Ebenen:


Kommunikation zwischen Raspberry PI und Laptop

rPI ist zu verstehen als Raspberry PI

Kommunikation zwischen ATmega32 und Raspberry PI

Port Belegung des ATmega32's:


Diskussion

Die Bauzeit des Roboters betrug ca. 150 Stunden, die Programmierung ausgeschlossen.

Der Aufbauprozess war relativ flüssig.

Während des Aufbauprozesses traten folgende Probleme auf:

- Hohe thermische Probleme und hoher Stromverbrauch:
  Aufgrund der Menge an Hardwarekomponenten entstanden beim Zusammenbau Platzprobleme, was zur Folge hatte das Abwärme schlecht entweichen konnte. Dazu kam noch das die Schaltregler und Linearregler mit zunehmenden Hardwarekomponenten höhere Lasten zu tragen hatten. Die Folge war das durch den Hitzestau teilweise im Roboter Temperaturen von über 100°C herrschten was zur Zerstörung einiger Bauelemente führte u.a. beim LM-7805. Das Problem konnte größtenteils durch eine Energiemanagement bewusste Programmierung behoben werden. Zusätzlich wurden einige Elemente durch energieeffizientere Komponenten ausgetauscht.
- Hohe Kamerastream Verzögerung:
  Bei geringer Netzwerkbandbreite trat eine sehr hohe Verzögerung des Kamerastreams auf: teilweise bis zu einer Minute. Die Folge war das ein Steuern des Roboters nahe zu unmöglich war. Durch das Deaktivieren des Streamcaches und verringern der FPS konnte das Auftreten der Verzögerung stark verringert werden.
- Erkennen des Abstürzen des Betriebssystem des Raspberry PI bei kurzzeitigem Spannungsabfall:
  Wenn die Akkuleistung zur Neige geht führt dies dazu dass das Betriebssystem des Raspberry PI abstürzt. Das Problem dabei war dass das Mikrocontroller Board seinen letzten Zustand behalten hat und z.B. immer weiter geradeaus gefahren ist. Durch einen externen Interrupt Pin am Mikrocontroller Board kann durch Setzen eines GPIO Pins am Raspberry PI verifiziert werden ob das Betriebssystem noch läuft.

Reflexion

Das Projekt lief sehr gut und die Entwicklung des Roboters ging zügig voran, da schon Erfahrungen bei der Programmierung vorhanden waren. Aber auch bei der Programmierung gab es Probleme: Unter anderem bei der Ultraschallsensor Programmierung entstanden Probleme aufgrund einer relativ komplexen Ansteuerung. Nach längerer Suche im Internet und häufigem Austesten wurde das Problem jedoch gelöst. Im Integrieren des Ultraschallsensors gab es die meisten Probleme auf Grund der unerfahrenen Bearbeitung. Es gab noch viele kleinere Probleme wie zum Beispiel die Ansteuerung der Infrarot-Sensoren, welche jedoch schnell gelöst werden konnten. Obwohl das Projekt sehr viele Funktionen hat, ist es noch erweiterbar und offen für viele weitere Funktionen.

Zukünftige Projekte

Ein weiteres Projekt könnte eine Oberflächenbearbeitung darstellen, bei welcher ein Kettenantrieb und eine Abdeckung der Hardware angebracht würden.

Erweiterungsmöglichkeiten

Das Projekt könnte durch eine Erweiterung um eine GUI programmierte Oberfläche einfacher zu steuern sein und auch bezüglich des Designs optimiert werden da zurzeit nur eine reine Konsolensteuerung möglich ist. Unter anderem könnte man eine Personen- und Gestenerkennung implementieren. Der Raspberry PI hätte dafür nicht genügend Leistung, jedoch könnte man den Kamerastream verwenden und diesen an einem leistungsstärkeren Rechner auswerten lassen, um anschließend die Ergebnisse wieder zurück an den Raspberry PI zu senden.

Literaturverzeichnis

Quellenangabe:

http://raspberrypiguide.de/howtos/raspberry-pi-gpio-how-to/

http://www.roboternetz.de/community/threads/62655-Raspberry-Pi-mit-Vb-net

http://www.mydealz.de/25645/raspberry-pi-modell-b-fur-30e-mini-rechner-zum-basteln/

https://www.google.com/search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

http://www.rasppishop.de/raspberry-pi-welt/erweiterungen/1/raspberry-pi-model-b-512mb-ram-rev.-2.0

https://github.com/2tata/BFGT-Roboter/blob/master/BFGTmega32-Board/Roboter.c

http://www.thingiverse.com/thing:36305/#files

http://markslaboratory.com/2013/04/mirroring-an-stl-for-makerware/

http://kampis-elektroecke.de/?page_id=3066

http://pymotw.com/2/socket/tcp.html

http://ipv6friday.org/blog/2011/11/ipv6addresses/

Anhang

(ToDo-Liste)

Stepp 1 Mikrocontroller

Was soll der Mikrocontroller können?

- I/O Steuerung

- ADW Steuerung

- PWM Steuerung

-I2C Steuerung

Stepp 2 Mikrocontroller > Raspberry PI

Wie soll der Mikrocontroller gesteuert werden?

- GPI/O Pins

- Serielle Steuerung

- I2C Steuerung

- JTAG Steuerung

Stepp 3 Raspberry PI Steuerung

Was soll der Raspberry PI können?

- Remote Interface spielen

- Server spielen

- Protokoll Sockel bilden

- Viertual Serial Com emulirung

- SFTP Server

- Netcat

- SSH

- TCP-/IP-Stack

- ?

Stepp 4 Raspberry PI remote Steuerung

Wie soll der Raspberry gesteuert werden Windows/Linux?

- C# Programm (Windows)

- Webinterface (OS unabhängig)

- C Programm (Linux)

- Java Programm (Windows und Linux)

- (Video Stream Implementierung ins Programm)

(Vorgangs liste)

Nr. | Vorgang | Dauer (Tage) | Vorgänger
1 | Informationen sammeln✔ | 1 | 1
2 | Dokumentation starten✔ | M | 1
3 | Mikrocontroller programmieren✔ | 8 | 3
4 | Verbindung mit Mikrocontroller und Raspberry Pi programmieren✔ | 5 | 3
5 | Raspberrysteuerung programmieren✔ | 10 | 5
6 | RPI Remotesteuerung (C#) (optional) | 13 | 6
7 | Infrarotdistanzsensoren auswerten (optional)✔ | 4 | 7
8 | Ansteuerung Servomotor über GPIO (optional)✔ | 3 | 7
9 | Realisierung von visueller Übertragung (optional)✔ | 7 | 7
10 | Ultraschallradar (optional)✔ | 15 | 10
11 | Sprachausgabe des Roboters (optional) | 10 | 10
12 | Alles ausführlich testen✔ | 2 | 4-12
13 | Hardware zusammenbauen (Endzustand)✔ | 1 | 13
15 | Dokumentation fertigstellen✔ | 3 | 15


(Projektstrukturplan)


(Fluss Diagramm)

Quellcode

(ATmega32)

/*

* uC_Serial.c

*

* Created: 15.01.2014 14:23:42

* Author: Jan-Tarek Butt

DDRA =||PA1|PA2|PA3|||||

DDRB =|PB0||PB2||PB4||PB6||

DDRC =|PC0|PC1|PC2|PC3|PC4|PC5|PC6|PC7|

DDRD =|PD0|PD1|PD2||PD4|PD5|PD6||

DC_Motor =PC2,PC3,PC4,PC5

Serial =PD0,PD1

externe Interrups =PD2

PWM =PD4,PD5

IR_Sensor =PA1,PA2,PA3

Ultraschall =PC0,PC7

Polulu =PB0,PB2,PB4,PB6

Serial übertragung =PC6

uC_aktiv =PC1

Lichtschranke =PD6

Schrittmotor =PB0,PB2,PB4,PB6

*/

#define F_CPU 16000000 // Taktfrequentz fest legen

#define BAUDRATE 57200 // Baudrate fuer die serielleschnittstelle fest legen

#include <avr/io.h>

#include <avr/sleep.h> // lib for Sleep mode

#include <avr/interrupt.h> // lib for Interrupts

#include <util/delay.h> // lib for delays

#include "BFGTmega32.h" // lib for Serial communication

int I_Wert; // ISR variable fuer serielle komunikation starten

int rPI; // ISR variable pruefen ob raspberry PI errechbar ist

int unsigned zaehler= 0; // ISR Timer0 variable fuer overflow benoetigt fuer Ultraschall Radar

ISR(INT0_vect) // Interrupt service routine loest aus wenn Raspberry errechtbar ist.

{

cli(); // Deaktiviren aller interrups

if (PIND & (1<<PD2)) // Wenn PD2 == High dann ...

{

rPI = 1; // rPI == Online

}else

{

rPI = 0; // rPI == Offline

}

sei(); // Aktiviren aller interrups

}

ISR(USART_RXC_vect) // Interrupt service routine loest aus wenn daten empfangen werden

{

cli(); // Deaktiviren aller interrups

while(bit_is_clear(UCSRA,RXC)); // warten auf Receive Complete

I_Wert = UDR;

sei(); // Aktiviren aller interrups

}

ISR (TIMER0_OVF_vect) // Interrupt service routine loest aus wenn timer0 Register ueberlaeuft

{

cli(); // Deaktiviren aller interrups

zaehler++;

sei(); // Aktiviren aller interrups

}

void Motor_richtung(int Motor_R, int Motor_L) // Motor richtungs steuerung

{

if (Motor_R == 1) // Rechter Motor

{

PORTC &= ~(1<<PC3);

PORTC |= (1<<PC2);

}

if (Motor_R == 2)

{

PORTC &= ~(1<<PC2);

PORTC |= (1<<PC3);

}

if (Motor_L == 3) // Linker Motor

{

PORTC &= ~(1<<PC5);

PORTC |= (1<<PC4);

}

if (Motor_L == 4)

{

PORTC &= ~(1<<PC4);

PORTC |= (1<<PC5);

}

if (Motor_R == 5 || Motor_L == 5) // Motoren Ausschalten

{

PORTC &= ~((1<<PC2)|(1<<PC3)|(1<<PC4)|(1<<PC5));

}

}

int SensorFront(void) // Messung Abstand Front

{

ADMUX |= (1 << MUX1); // PA2 fuer AD wandlung EIN

ADCSRA |= (1 << ADSC); // AD-Wandlung starten

_delay_us(500);

int IR[4] = {0,ADCW,0,0}; // AD-Wandlung 10-Bit

ADCSRA |= (1 << ADSC); // AD-Wandlung starten

_delay_us(500);

IR[2] = ADCW; // AD-Wandlung 10-Bit

ADCSRA |= (1 << ADSC); // AD-Wandlung starten

_delay_us(500);

IR[3] = ADCW; // AD-Wandlung 10-Bit

IR[0] = ((IR[1]+IR[2]+IR[3])/3); // Mittlung der AD-Wandlung

ADMUX &= ~(1 << MUX1); // PC2 fuer AD wandlung AUS

double d = ((1 - ((IR[0] * 0.0048828125) * (1.0 / 18.0))) / ((IR[0] * 0.0048828125) * (2.0 / 27.0)))*2; // Distanz Umrechnung in cm

if (d < 5) // Wenn d kleiner als 5 dann ...

d = 400; // Minimum 5cm, Meldung 400

else if (d > 50) // Wenn d größer als 50 dann ...

d = 300; // Maximum 50cm, Meldung 300

return d; // Rückgabe d

}

int SensorRechts(void) // Messung Abstand Rechts

{

ADMUX |= ((1 << MUX0)|(1 << MUX1)); // PA3 für AD wandlung EIN

ADCSRA |= (1 << ADSC); // AD-Wandlung starten

_delay_us(500);

int IR[4] = {0,ADCW,0,0}; // AD-Wandlung 10-Bit

ADCSRA |= (1 << ADSC); // AD-Wandlung starten

_delay_us(500);

IR[2] = ADCW; // AD-Wandlung 10-Bit

ADCSRA |= (1 << ADSC); // AD-Wandlung starten

_delay_us(500);

IR[3] = ADCW; // AD-Wandlung 10-Bit

IR[0] = ((IR[1]+IR[2]+IR[3])/3); // Mittlung der AD-Wandlung

ADMUX &= ~((1 << MUX0)|(1 << MUX1)); // PC3 für AD wandlung AUS

double d = ((1 - ((IR[0] * 0.0048828125) * (1.0 / 18.0))) / ((IR[0] * 0.0048828125) * (2.0 / 14.0)))*2; // Distanz Umrechnung in cm

if (d < 5) // Wenn d kleiner als 5 dann ...

d = 400; // Minimum 5cm, Meldung 400

else if (d > 50) // Wenn d größer als 50 dann ...

d = 300; // Maximum 50cm, Meldung 300

return d; // Rückgabe d

}

int SensorLinks(void) // Messung Abstand Links

{

ADMUX |= (1 << MUX0); // PA1 für AD wandlung EIN

ADCSRA |= (1 << ADSC); // AD-Wandlung starten

_delay_us(500);

int IR[4] = {0,ADCW,0,0}; // AD-Wandlung 10-Bit

ADCSRA |= (1 << ADSC); // AD-Wandlung starten

_delay_us(500);

IR[2] = ADCW; // AD-Wandlung 10-Bit

ADCSRA |= (1 << ADSC); // AD-Wandlung starten

_delay_us(500);

IR[3] = ADCW; // AD-Wandlung 10-Bit

IR[0] = ((IR[1]+IR[2]+IR[3])/3); // Mittlung der AD-Wandlung

ADMUX &= ~(1 << MUX0); // PC4 für AD wandlung AUS

double d = ((1 - ((IR[0] * 0.0048828125) * (1.0 / 18.0))) / ((IR[0] * 0.0048828125) * (2.0 / 12.0)))*2; // Distanz Umrechnung in cm

if (d < 5) // Wenn d kleiner als 5 dann ...

d = 400; // Minimum 5cm, Meldung 400

else if (d > 50) // Wenn d größer als 50 dann ...

d = 300; // Maximum 50cm, Meldung 300

return d; // Rückgabe d

}

int Usensor(void) // Messung Ultraschall Sensor

{

PORTC |= (1<<PC0);

_delay_us(10);

PORTC &= ~(1<<PC0); // Ultraschall Trigger ausloesen

while((PINC&(1<<PC7))==0); // Wartet auf Steigene Flanke

TCCR0 |= (1<<CS01); // Timer0 mit Prescale von 8 starten

while(PINC&(1<<PC7)); // Warten solange Echo High

TCCR0 = 0; // Timer0 Stoppen

double t = (((zaehler<<8)+TCNT0)/2)*0.5; // zeit in us umrechnen

unsigned int s = (0.0343*t); // Distanz in cm berechnen

zaehler=0; // Timer 0 Overflow auf Null setzen

uart_send_string(" UL:");

uart_send_int(s,1);

uart_send_string(" "); // Serielle ausgaben von Ultraschall werten

_delay_ms(1);

return 0;

}

int SchrittMotor(void) // Schrittmotor steuerung fuer Ultraschall Radar

{

PORTB &= ~(1<<PB0); // Schrittmotor Endstufe ENABLE

PORTB |= (1<<PB4);

_delay_ms(5);

PORTB &= ~(1<<PB4);

_delay_ms(5); // Ein step vorwaerst

PORTB |= (1<<PB0); // Schrittmotor Endstufe DIESABLE

int Smotor = 0;

if (PIND & (1<<PD6)) // Wenn Lichtschranke ausloest dann ...

{

Smotor = 1;

}

Usensor(); // Ultraschall Messung Ausloesen

return Smotor;

}

int Sensor_Ausgabe(void) //Ausgabe der Sensoren

{

int Sensoren[4]={SensorFront(),SensorRechts(),SensorLinks(),SchrittMotor()}; // Array, Sensoren auslesen

uart_send_string("SF:");

uart_send_int(Sensoren[0],1); // Infrarot Front Sensor ausgeben

uart_send_string(" SR:");

uart_send_int(Sensoren[1],1); // Infrarot Rechter Sensor ausgeben

uart_send_string(" SL:");

uart_send_int(Sensoren[2],1); // Infrarot Linker Sensor ausgeben

uart_send_string(" SM:");

uart_send_int(Sensoren[3],1); // Schrittmotor Referrers signal der Lichtschranke ausgeben

uart_send_string("\n\r"); // Zeielnumbruch

_delay_ms(1);

return 0;

}

int main(void)

{

uart_init(); // Serial Inizialisirung

DDRC = 0b01111111;

DDRB = 0b11111111;

DDRA = 0b11110001;

DDRD &= ~((1 << PD2)|(1<<PD6)); // INT0 und Lichtschranke input...

DDRD |= (1<<PD4)|(1<<PD5); // PWM Ausgaenge festlegen

ADCSRA = 0b10000111; // Prescaler 128

ADMUX |= (1<<REFS0); // 5V Referrens spannung

TCCR1A |= (1<<WGM10)|(1<<COM1A1)|(1<<COM1B1);

TCCR1B |= (1<<WGM12)|(1<<CS12); // Prescaler 256

GICR |= (1<<INT0); // IRS INT0 externer Interrupt aktiviren

MCUCR |= (1<<ISC00); // ISR INT0 Reaktion auf jede aenderung

PORTB |= ((1<<PB0)|(1<<PB6)); // Schrittmotor Endstufe aus schalten

TIMSK |= (1<<TOIE0); // Timer0 Overflow Interrupt erlauben

while(1)

{

sei(); // Aktiviren aller interrups

uart_init(); // Serial Inizialisirung

if (rPI == 1) // Wenn INT0 == High dann ...

{

PORTC |= (1<<PC1);

Sensor_Ausgabe(); // Pereperie auswerten

if (I_Wert == 49) // Wenn eingabe == 49 dann ...

{

cli(); // Deaktiviren aller interrups

I_Wert = 0;

PORTC |= (1<<PC6); // anzeigen das daten jetzt uebertragen werden koennen

int Motor_R = (uart_get_int()-48); // Richtungs vorgabe der Motoren 1-2 Vor-Rueckwaerts 5 = Motoren Aus

int Motor_L = (uart_get_int()-48); // Richtungs vorgabe der Motoren 3-4 Vor-Rueckwaerts 5 = Motoren Aus

if(Motor_R > 5 || Motor_L > 5) // Wenn eingabe größer als 5 dann ...

{

PORTC &= ~(1<<PC6); // anzeigen das daten nicht mehr uebertragen werden koennen

return main(); // Zurueck an denn anfang der main funktion

}

if(Motor_R == 5 || Motor_L == 5) // Wenn eingabe == 5 dann ...

{

Motor_richtung(Motor_R,Motor_L); // uebergabe an Motor_richtung

PORTC &= ~(1<<PC6); // anzeigen das daten nicht mehr uebertragen werden koennen

return main(); // Zurueck an denn anfang der main funktion

}

int PWM[4] = {0,(uart_get_int()-48),(uart_get_int()-48),(uart_get_int()-48)}; // Annahmen der Motor geschwindigkein 0-255

PWM[0] = (PWM[1]*100+PWM[2]*10+PWM[3]);

int PWM1[4] = {0,(uart_get_int()-48),(uart_get_int()-48),(uart_get_int()-48)}; // Annahmen der Motor geschwindigkein 0-255

PWM1[0] = (PWM1[1]*100+PWM1[2]*10+PWM1[3]);

if (PWM[0] <= 255 && PWM1[0] <= 255) // Wenn PWM kleiner als 255 dann ...

{

uart_send_string("MR: ");

uart_send_int(Motor_R,1);

uart_send_string(" ");

uart_send_int(PWM[0],1);

uart_send_string("\n\r"); // Sende zeielnumbruch

uart_send_string("ML: ");

uart_send_int(Motor_L,1);

uart_send_string(" ");

uart_send_int(PWM1[0],1);

uart_send_string("\n\r"); // Sende zeielnumbruch

if ((uart_get_int()-48) == 1) // Bestaetigung der uebertragenen werte wenn eingabe == 1 dann ...

{

Motor_richtung(Motor_R,Motor_L);

OCR1B = PWM[0]; // PWM setzen

OCR1A = PWM1[0]; // PWM setzen

}

}

PORTC &= ~(1<<PC6); // anzeigen das daten nicht mehr uebertragen werden koennen

}else

{

PORTC &= ~(1<<PC6); // anzeigen das daten nicht mehr uebertragen werden koennen

}

}

else

{

PORTC &= ~(1<<PC1);

Motor_richtung(5,5); // uebergabe an Motor_richtung

set_sleep_mode(SLEEP_MODE_IDLE); // sleep mode Aktiviren

sleep_mode(); // uC geht Ideln

}

}

}

(Raspberry PI)

#!/bin/bash

# Raspbarry PI Server zur Steuerung des Roboters

# Autor: Jan-Tarek Butt

# Datum: 12.03.2014

clear

PORT=4444

BAUTRATE=57600

SCHNITSTELLE="/dev/ttyUSB0"

LP_ADRESSE="fe80::223:aeff:fe42:21b1%wlan0"

LP_PORT=4445

echo "Server start..."

while true

do

stty -F $SCHNITSTELLE raw ispeed $BAUTRATE ospeed $BAUTRATE cs8 -ignpar -cstopb -echo

COMMAND=$( nc -6lp $PORT )

echo $COMMAND

read -i -s Line < /dev/ttyUSB0

echo $Line

if [ "$COMMAND" == "1" ]; then

raspivid -w 640 -h 480 -t 999999 -fps 10 -b 4000000 -o - | nc -6 fe80::223:14ff:fee1:aa80%wlan0 5001 &

fi;

if [ "$COMMAND" == "s" ]; then

echo -n "1" >$SCHNITSTELLE

echo -n "2" >$SCHNITSTELLE

echo -n "3" >$SCHNITSTELLE

echo -n "255" >$SCHNITSTELLE

echo -n "255" >$SCHNITSTELLE

echo -n "1" >$SCHNITSTELLE

fi;

if [ "$COMMAND" == "w" ]; then

echo -n "1" >$SCHNITSTELLE

echo -n "1" >$SCHNITSTELLE

echo -n "4" >$SCHNITSTELLE

echo -n "255" >$SCHNITSTELLE

echo -n "255" >$SCHNITSTELLE

echo -n "1" >$SCHNITSTELLE

fi;

if [ "$COMMAND" == "d" ]; then

echo -n "1" >$SCHNITSTELLE

echo -n "2" >$SCHNITSTELLE

echo -n "3" >$SCHNITSTELLE

echo -n "255" >$SCHNITSTELLE

echo -n "000" >$SCHNITSTELLE

echo -n "1" >$SCHNITSTELLE

fi;

if [ "$COMMAND" == "a" ]; then

echo -n "1" >$SCHNITSTELLE

echo -n "2" >$SCHNITSTELLE

echo -n "3" >$SCHNITSTELLE

echo -n "000" >$SCHNITSTELLE

echo -n "255" >$SCHNITSTELLE

echo -n "1" >$SCHNITSTELLE

fi;

if [ "$COMMAND" == "q" ]; then

echo -n "1" >$SCHNITSTELLE

echo -n "5" >$SCHNITSTELLE

echo -n "5" >$SCHNITSTELLE

fi;

done

Rasperry PI Kamerasteuerung

# Kamera Servo steuerung

# Autor: Jan-Tarek Butt

# Datum: 12.03.2014

import RPi.GPIO as GPIO

import time

import os

# Pin 26 als Ausgang deklarieren

GPIO.setwarnings(False)

GPIO.setmode(GPIO.BOARD)

GPIO.setup(26, GPIO.OUT)

while True:

# PWM mit 50Hz an Pin 26 starten

Servo = GPIO.PWM(26, 50)

# Richtungseingabe

Eingabe = raw_input("Bitte treffen Sie Ihre Wahl: ")

# Richtung "Rechts"

if(Eingabe == "r"):

# Schrittweite eingeben

Schritte = raw_input("Schrittweite: ")

print Schritte, "Schritte nach Rechts"

# PWM mit 10% Dutycycle (2ms) generieren

Servo.start(10)

for Counter in range(int(Schritte)):

time.sleep(0.01)

# PWM stoppen

Servo.stop()

# Mittelstellung einnehmen

elif(Eingabe == "m"):

Servo.start(7)

print "Drehung in die Mitte"

time.sleep(1)

Servo.stop()

# Richtung "Links"

elif(Eingabe == "l"):

# Schrittweite eingeben

Schritte = raw_input("Schrittweite: ")

print Schritte, "Schritte nach Links"

# PWM mit 5% Dutycycle (1ms) generieren

Servo.start(5)

for Counter in range(int(Schritte)):

time.sleep(0.01)

# PWM stoppen

Servo.stop()

# Programm beenden

elif(Eingabe == "q"):

print "Programm wird beendet......"

os._exit(1)

Servo.stop()

GPIO.cleanup()

# Ungueltige Eingabe

else:

print "Ungueltige Eingabe!"

(Roboter Steuerungs Skript)

#!/bin/bash

clear

RPI_WLAN_IPV6=fe80::9644:52ff:fe04:2db6

RPI_ETH_IPV6=fe80::ba27:ebff:fecd:5984

PORT=4444

LP_PORT=4445

W_INTERFACE=wlan0

E_INTERFACE=eth0

STATUS=0

echo "Ping test..."

ping6 -c 1 $RPI_WLAN_IPV6%$W_INTERFACE

WLANW=$?

ping6 -c 1 $RPI_WLAN_IPV6%$E_INTERFACE

WLANE=$?

ping6 -c 1 $RPI_ETH_IPV6%$E_INTERFACE

ETHE=$?

ping6 -c 1 $RPI_ETH_IPV6%$W_INTERFACE

ETHW=$?

if [ $WLANW -ne 0 -a $WLANE -ne 0 -a $ETHE -ne 0 -a $ETHW -ne 0 ]; then

echo "Roboter nicht errechtbar!"

exit

fi;

if [ $WLANW -eq 0 ]; then

INTERFACE="$RPI_WLAN_IPV6%$W_INTERFACE"

echo "Wlan verbindung"

fi;

if [ $WLANE -eq 0 ]; then

INTERFACE="$RPI_WLAN_IPV6%$E_INTERFACE"

echo "Wlan verbindung"

fi;

if [ $ETHE -eq 0 ]; then

INTERFACE="$RPI_ETH_IPV6%$E_INTERFACE"

echo "Lan verbindung"

fi;

if [ $ETHW -eq 0 ]; then

INTERFACE="$RPI_ETH_IPV6%$W_INTERFACE"

echo "Lan verbindung"

fi;

echo "Befel eingeben:"

while true

do

read -n 1 -s COMMAND

echo $COMMAND

if [ "$COMMAND" == "1" ]; then

nc -6lp 5001 | mplayer -fps 15 -cache 512 - &

sleep 1

echo "1" | nc -6 $INTERFACE $PORT

fi;

if [ "$COMMAND" == "w" ]; then

echo $COMMAND | nc -6 $INTERFACE $PORT

fi;

if [ "$COMMAND" == "s" ]; then

echo $COMMAND | nc -6 $INTERFACE $PORT

fi;

if [ "$COMMAND" == "a" ]; then

echo $COMMAND | nc -6 $INTERFACE $PORT

fi;

if [ "$COMMAND" == "d" ]; then

echo $COMMAND | nc -6 $INTERFACE $PORT

fi;

if [ "$COMMAND" == "q" ]; then

echo $COMMAND | nc -6 $INTERFACE $PORT

fi;

done

Netzwerk gesteuerter Roboter

Dokumentation Mikrocontroller über Ethernet

Projektkurs: microcontroller über ethernet Theis Ammermann, Jan-tarek butt. sören j,tobias b

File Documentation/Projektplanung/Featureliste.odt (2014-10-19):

Fahrzeug/Roboter

Feature List

-Spannungsteiler (Messgerät)

-Amperemeter

-Ultraschallradar Done

-Schrittmotor (klein) Done

-Pololu-Schrittmotortreiber Done

-Lichtschranke Done

-Ultraschallsensor Done

-Schleifkontakte

-Kamerahaltung konstruieren (CAD) Done

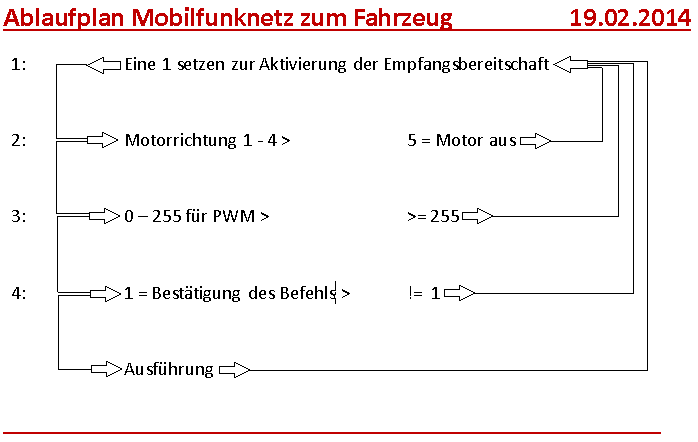
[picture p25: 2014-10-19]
Documentation/images/AblaufplanMobilfunknetz.png

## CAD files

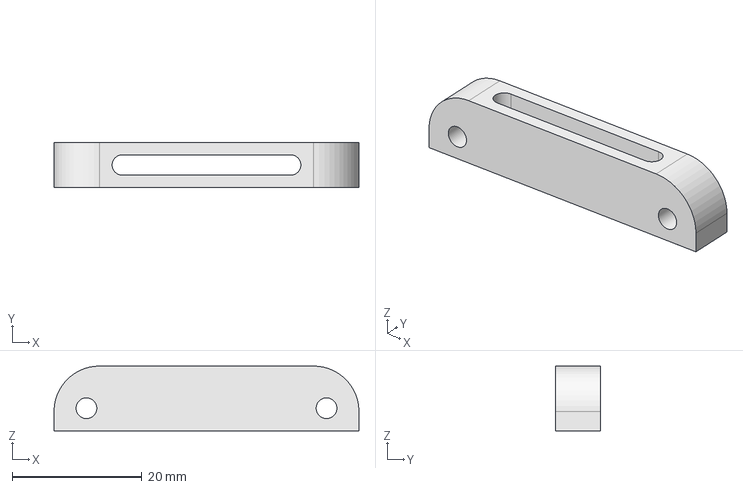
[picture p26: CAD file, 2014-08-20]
CAD/IR-Sensorhalter/IR-Sensorhalter.fcstd
47.0 x 7.00 x 10.0 mm

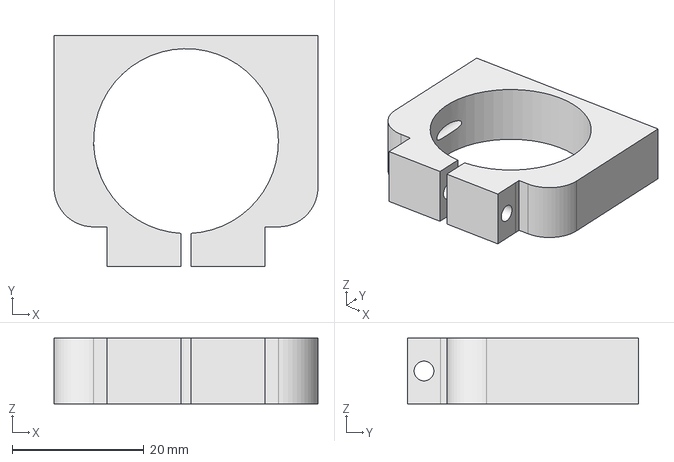
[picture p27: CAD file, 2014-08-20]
CAD/Rad_Halterung/Rad_halterung.fcstd
40.0 x 35.0 x 10.0 mm

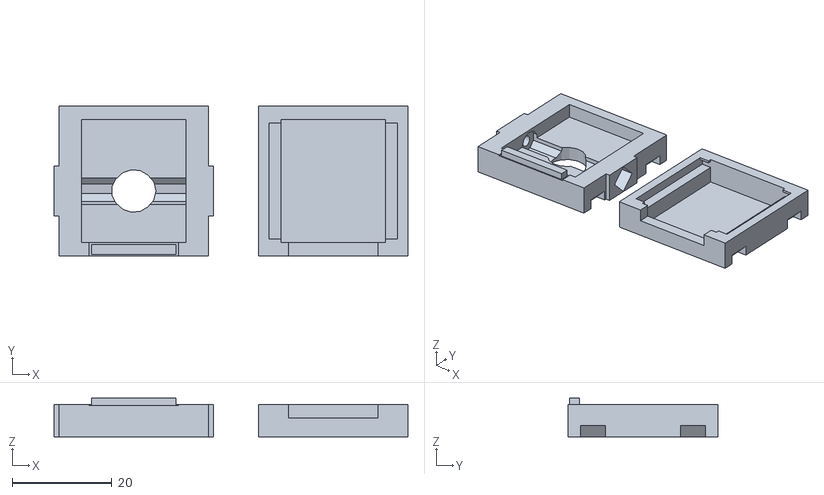
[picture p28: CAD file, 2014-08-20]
CAD/rpi_camera halterung/pi_cam_micro_servo_case.stl
71.0 x 30.0 x 7.75

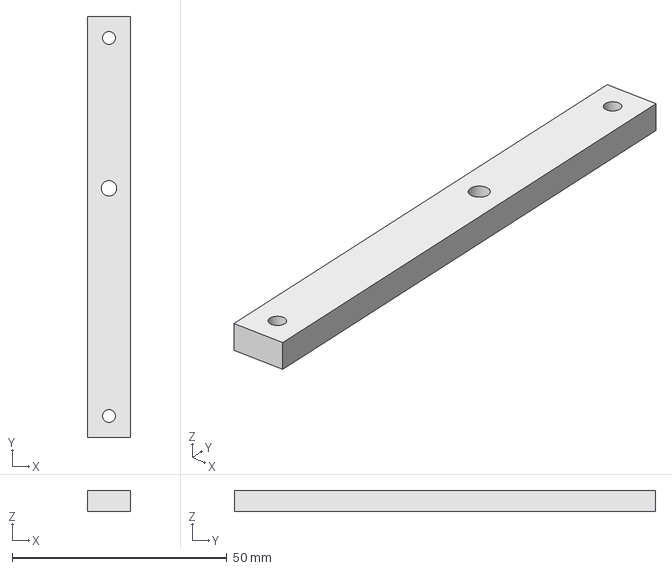
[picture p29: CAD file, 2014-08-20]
CAD/rpi_Halterung/Rasberry_Halterung_A.fcstd
10.0 x 98.0 x 5.00 mm

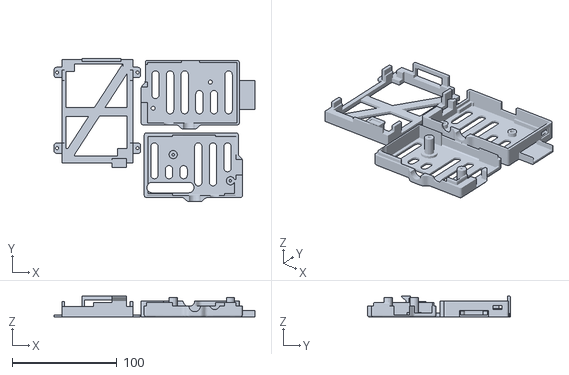
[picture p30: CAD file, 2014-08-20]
CAD/rpi_huelle/raspberry_pi_cover__9_.stl
192.3 x 137.2 x 20.0

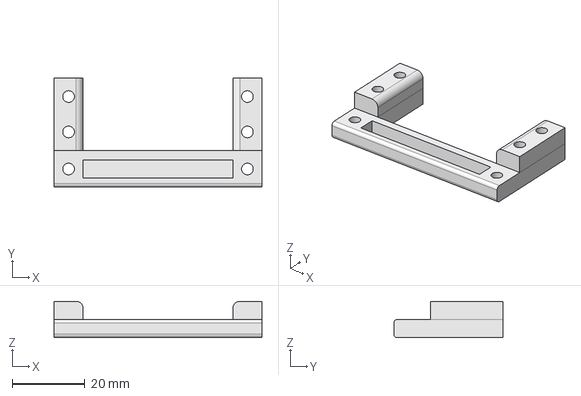
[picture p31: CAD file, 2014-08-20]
CAD/Servo_Halterung/Servo_Halterung_v1.fcstd
57.0 x 30.0 x 10.0 mm

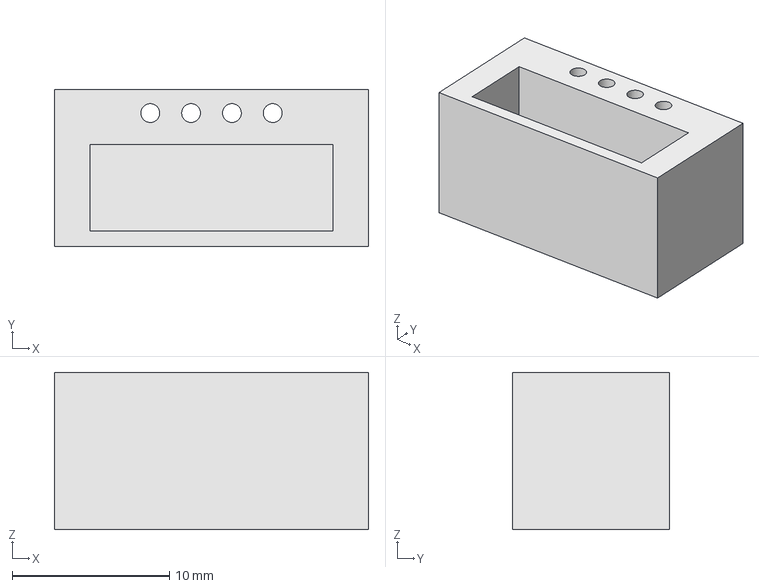
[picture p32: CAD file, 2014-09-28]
CAD/Ultraschall_Radar_Halterung/Ultraschall_Radar_Kopf.fcstd
20.0 x 10.0 x 10.0 mm

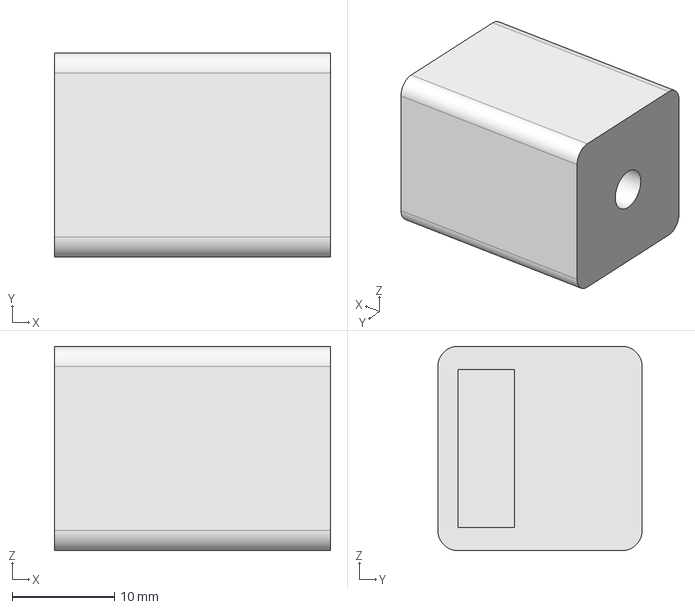
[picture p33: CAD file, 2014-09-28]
CAD/Ultraschall_Radar_Halterung/Ultraschall_Radar_Kopplung.fcstd
27.0 x 20.0 x 20.0 mm

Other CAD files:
CAD/Grundplatte/Roboter_Grundplatte.fcstd
CAD/Raeder/rad.fcstd
CAD/Rad_Halterung/Rad_halterung_v2.stl
CAD/rpi_Halterung/Rasberry_Halterung_B.fcstd
CAD/rpi_Halterung/Rasberry_Halterung_A_v1.stl
CAD/rpi_Halterung/Rasberry_Halterung_B_v1.stl
CAD/IR-Sensorhalter/IR-Sensorhalter.stl
CAD/Rad_Halterung/Rad_halterung.stl
CAD/Servo_Halterung/Servo_Halterung_v1.stl
CAD/Ultraschall_Radar_Halterung/Ultraschall_Radar_Kopf.stl
CAD/Ultraschall_Radar_Halterung/Ultraschall_Radar_Kopplung.stl

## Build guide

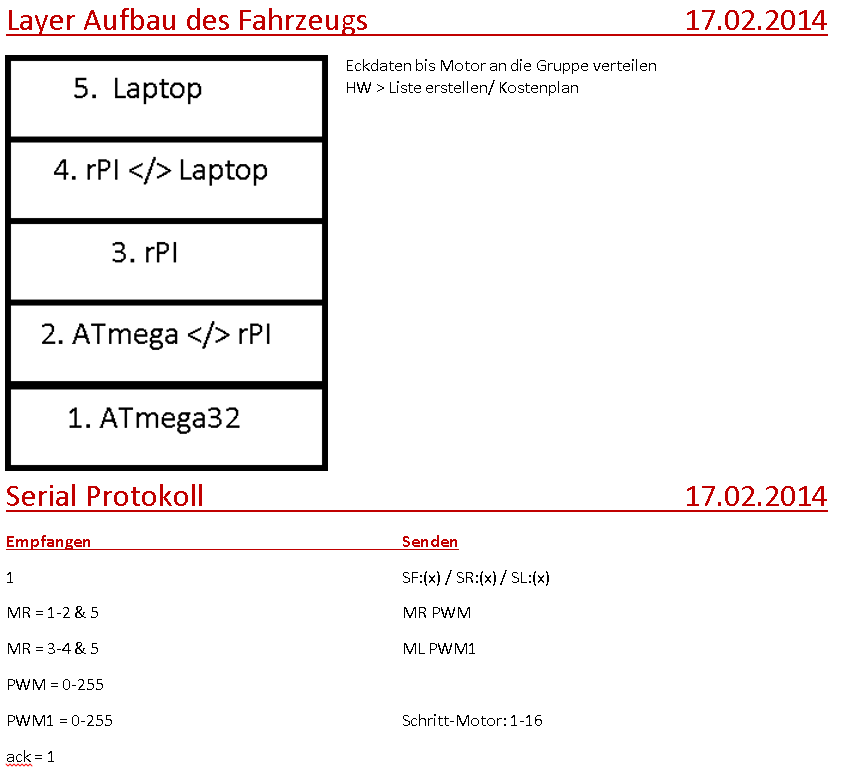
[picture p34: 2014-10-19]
Documentation/images/LayerAufbau17022014.png

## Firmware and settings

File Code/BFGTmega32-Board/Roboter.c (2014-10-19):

/*
 * Roboter.c
 *
 * Created: 15.01.2014 14:23:42
 *  Author: Jan-Tarek Butt
 ----------------------------------------------
 DDRA =||PA1|PA2|PA3|||||
 DDRB =|PB0||PB2||PB4||PB6||
 DDRC =|PC0|PC1|PC2|PC3|PC4|PC5|PC6|PC7|
 DDRD =|PD0|PD1|PD2||PD4|PD5|PD6||
 
 IR_Sensor				=PA1,PA2,PA3
 Schrittmotor			=PB0,PB2,PB4,PB6
 DC_Motor				=PC2,PC3,PC4,PC5
 Ultraschall			=PC0,PC7
 Serial uebertragung	=PC6
 uC_aktiv				=PC1
 Serial					=PD0,PD1
 PWM					=PD4,PD5
 externe Interrups		=PD2
 Schrittmotor Endstop	=PD6
  ----------------------------------------------
 */
#define F_CPU 16000000			// Define clock speed
#define BAUDRATE 57200			// Baudrate fuer die serielleschnittstelle fest legen
//------------Ultraschall Sensor Konfiguration--------------
#define ZAELERTRIGGER 10		// Ultraschall trigger signal maximum Overfow limmit für Timer0
#define	ZAELERECHO 300			// Ultraschall echo signal maximum Overfow limmit für Timer0

#include <avr/io.h>
#include <avr/sleep.h>			// lib for Sleep mode
#include <avr/interrupt.h>		// lib for Interrupts
#include <util/delay.h>			// lib for delays
#include "BFGTmega32.h"			// lib for Serial communication

int I_Wert;						// ISR variable fuer serielle komunikation starten
int rPI;						// ISR variable pruefen ob raspberry PI errechbar ist
int unsigned zaehler= 0;		// ISR Timer0 variable fuer overflow benoetigt fuer Ultraschall Radar
int ulHistory[2] = {0,0};		// Ultraschall Sensor History
int stepperRound= 0;			// counter for stepper driver
int firstStart = 1;				// Kallibrier variable fuer das Ultraschall Radar
int waitRound = 0;				// Stepperdriver delay
int ulio = 0;					// IO für das Ultraschall Radar
int irio = 0;					// IO für die Infrarot sensoren


ISR(INT0_vect) // Interrupt service routine loest aus wenn Raspberry errechtbar ist.
{
	cli();					// Deaktiviren aller interrups
	if (PIND & (1<<PD2))	// Wenn PD2 == High dann ...
	{
		rPI = 1;			// rPI == Online
	}else
	{
		rPI = 0;			// rPI == Offline
	}
	sei();					// Aktiviren aller interrups
}

ISR(USART_RXC_vect)	// Interrupt service routine loest aus wenn daten empfangen werden
{
	cli();								// Deaktiviren aller interrups
	while(bit_is_clear(UCSRA,RXC));		// warten auf Receive Complete
	I_Wert = UDR;
	sei();								// Aktiviren aller interrups
}

ISR (TIMER0_OVF_vect) // Interrupt service routine loest aus wenn timer0 Register ueberlaeuft
{
	cli();			// Deaktiviren aller interrups
	zaehler++;
	sei();			// Aktiviren aller interrups
}

void Motor_richtung(int Motor_R, int Motor_L) // Motor richtungs steuerung
{
	if (Motor_R == 1)					// Rechter Motor
	{
		PORTC &= ~(1<<PC3);
		PORTC |= (1<<PC2);
	}
	if (Motor_R == 2)
	{
		PORTC &= ~(1<<PC2);
		PORTC |= (1<<PC3);
	}
	if (Motor_L == 3)					// Linker Motor
	{
		PORTC &= ~(1<<PC5);
		PORTC |= (1<<PC4);
	}
	if (Motor_L == 4)
	{
		PORTC &= ~(1<<PC4);
		PORTC |= (1<<PC5);
	}
	if (Motor_R == 5 || Motor_L == 5)	// Motoren Ausschalten
	{
		PORTC &= ~((1<<PC2)|(1<<PC3)|(1<<PC4)|(1<<PC5));
	}
}

int SensorRechts(void) // Messung Abstand Rechts
{
	ADMUX |= (1 << MUX0);						// PA1 fuer AD wandlung EIN
	ADCSRA |= (1 << ADSC);						// AD-Wandlung starten
	_delay_us(500);
	int IR[4] = {0,(ADCL+(256*ADCH)),0,0};		// AD-Wandlung 10-Bit
	ADCSRA |= (1 << ADSC);						// AD-Wandlung starten
	_delay_us(500);
	IR[2] = (ADCL+(256*ADCH));					// AD-Wandlung 10-Bit
	ADCSRA |= (1 << ADSC);						// AD-Wandlung starten
	_delay_us(500);
	IR[3] = (ADCL+(256*ADCH));					// AD-Wandlung 10-Bit
	IR[0] = ((IR[1]+IR[2]+IR[3])/3);			// Mittlung der AD-Wandlung
	ADMUX &= ~(1 << MUX0);						// PC4 fuer AD wandlung AUS
	double d = ((1 - ((IR[0] * 0.0048828125) * (1.0 / 18.0))) / ((IR[0] * 0.0048828125) * (2.0 / 27.0)))*2;	// Distanz Umrechnung in cm fuer SHARP 2Y0A12 F 11
	if (d < 7)									// Wenn d kleiner als 5 dann ...
	d = 400;									// Minimum 5cm, Meldung 400
	else if (d > 50)							// Wenn d groeßer als 50 dann ...
	d = 300;									// Maximum 50cm, Meldung 300
	return d;									// Rueckgabe d
}

int SensorFront(void) // Messung Abstand Front
{
	ADMUX |= (1 << MUX1);					// PA2 fuer AD wandlung EIN
	ADCSRA |= (1 << ADSC);					// AD-Wandlung starten
	_delay_us(500);
	int IR[4] = {0,(ADCL+(256*ADCH)),0,0};	// AD-Wandlung 10-Bit
	ADCSRA |= (1 << ADSC);					// AD-Wandlung starten
	_delay_us(500);
	IR[2] = (ADCL+(256*ADCH));				// AD-Wandlung 10-Bit
	ADCSRA |= (1 << ADSC);					// AD-Wandlung starten
	_delay_us(500);
	IR[3] = (ADCL+(256*ADCH));				// AD-Wandlung 10-Bit
	IR[0] = ((IR[1]+IR[2]+IR[3])/3);		// Mittlung der AD-Wandlung
	ADMUX &= ~(1 << MUX1);					// PC2 fuer AD wandlung AUS(2.0 / 27.0)
	double d = ((1 - ((IR[0] * 0.0048828125) * (1.0 / 18.0))) / ((IR[0] * 0.0048828125) * (2.0 / 14.0)))*2;	// Distanz Umrechnung in cm fuer SHARP 2D120XF 9Z
	if (d < 5)								// Wenn d kleiner als 5 dann ...
	d = 400;								// Minimum 5cm, Meldung 400
	else if (d > 50)						// Wenn d groeßer als 50 dann ...
	d = 300;								// Maximum 50cm, Meldung 300
	return d;								// Rueckgabe d
}

int SensorLinks(void) // Messung Abstand Links
{
	ADMUX |= ((1 << MUX0)|(1 << MUX1));		// PA3 fuer AD wandlung EIN
	ADCSRA |= (1 << ADSC);					// AD-Wandlung starten
	_delay_us(500);
	int IR[4] = {0,(ADCL+(256*ADCH)),0,0};	// AD-Wandlung 10-Bit
	ADCSRA |= (1 << ADSC);					// AD-Wandlung starten
	_delay_us(500);
	IR[2] = (ADCL+(256*ADCH));				// AD-Wandlung 10-Bit
	ADCSRA |= (1 << ADSC);					// AD-Wandlung starten
	_delay_us(500);
	IR[3] = (ADCL+(256*ADCH));				// AD-Wandlung 10-Bit
	IR[0] = ((IR[1]+IR[2]+IR[3])/3);		// Mittlung der AD-Wandlung
	ADMUX &= ~((1 << MUX0)|(1 << MUX1));	// PC3 fuer AD wandlung AUS
	double d = ((1 - ((IR[0] * 0.0048828125) * (1.0 / 18.0))) / ((IR[0] * 0.0048828125) * (2.0 / 12.0)))*2;	// Distanz Umrechnung in cm fuer SHARP 0A41SK F 33
	if (d < 5)								// Wenn d kleiner als 5 dann ...
	d = 400;								// Minimum 5cm, Meldung 400
	else if (d > 50)						// Wenn d groeßer als 50 dann ...
	d = 300;								// Maximum 50cm, Meldung 300
	return d;								// Rueckgabe d
}

int Usensor(void) // Messung Ultraschall Sensor
{
	int s = 0;
	PORTC |= (1<<PC0);
	_delay_us(10);
	PORTC &= ~(1<<PC0);					// Ultraschall Trigger ausloesen
	TCCR0 |= (1<<CS01);					// Timer0 mit Prescale von 8 starten
	while(!(PINC&(1<<PC7)))				// Wartet auf Steigene Flanke
	{
		_delay_us(0);
		if(zaehler >= ZAELERTRIGGER)
			break;
	}
	TCCR0 &= ~(1<<CS01);				//Timer Stoppen
	if(!(zaehler >= ZAELERTRIGGER))
	{
		zaehler = 0;
		TCCR0 |= (1<<CS01);				// Timer0 mit Prescale von 8 starten
		while(PINC&(1<<PC7))			// Warten solange Echo High
		{
			_delay_us(0);
			if(zaehler >= ZAELERECHO)
				break;
		}
		TCCR0 &= ~(1<<CS01);			//Timer Stoppen
		if (!(zaehler >= ZAELERECHO))
		{
			double t = (((zaehler<<8)+TCNT0)/2)*0.5;
			s = (0.0343*t);
			ulHistory[0] = ulHistory[1];
			ulHistory[1]= s;
		}
		else
		{
			s = ((ulHistory[0]+ulHistory[1])/2);
		}
	}
	else
	{
		s = ((ulHistory[0]+ulHistory[1])/2);
	}
	zaehler = 0;
	return s;
}

int SchrittMotor(void) // Schrittmotor steuerung fuer Ultraschall Radar
{
	PORTB &= ~(1<<PB0);				// Schrittmotor Endstufe ENABLE
	if (firstStart == 1)
	{
		firstStart = 0;
		while (stepperRound < 24)
		{
			if (!(PIND & (1<<PIND6)))
			{
				stepperRound ++;
			} else
			{
				PORTB |= (1<<PB4);
				_delay_ms(20);
				PORTB &= ~(1<<PB4);
				_delay_ms(200);
				stepperRound ++;
			}
		}
		stepperRound = 0;
		PORTB &= ~(1<<PB6);			// Dir Low
	}
	if (stepperRound < 24)
	{
		stepperRound ++;
		PORTB |= (1<<PB4);
		_delay_ms(2);
		PORTB &= ~(1<<PB4);
		if (!(PIND & (1<<PIND6)) && stepperRound >= 3)
		{
			stepperRound = 24;
			_delay_ms(10);
		}
	}
	else
	{
		if (waitRound == 0)
		{
			_delay_ms(100);
			waitRound = 1;
		}
		PORTB |= (1<<PB6);			// Dir High
		stepperRound ++;
		PORTB |= (1<<PB4);
		_delay_ms(2);
		PORTB &= ~(1<<PB4);
		if (!(PIND & (1<<PIND6)) && stepperRound >= 27)
		{
			stepperRound = 49;
			_delay_ms(10);
		}
	}
	_delay_ms(2);
	if (stepperRound >= 48)
	{
		stepperRound = 0;
		waitRound = 0;
		_delay_ms(100);
		PORTB &= ~(1<<PB6);			// Dir low
	}
	_delay_ms(2);
	int ul = Usensor();
	if (ul <= 10)
	{
		_delay_ms(10);
	}
	uart_send_string("	UL:");
	uart_send_int(ul,2);
	uart_send_string("	SM:");
	return stepperRound;
}

int Sensor_Ausgabe(void) //Ausgabe der Sensoren
{
	if (irio == 1)
	{
		uart_send_string("SR:");
		uart_send_int(SensorRechts(),2);		// Infrarot Front Sensor ausgeben
		uart_send_string("	SF:");
		uart_send_int(SensorFront(),2);			// Infrarot Rechter Sensor ausgeben
		uart_send_string("	SL:");
		uart_send_int(SensorLinks(),2);			// Infrarot Linker Sensor ausgeben
	}
	if (ulio == 1)
	{
		uart_send_int(SchrittMotor(),2);		// Schrittmotor Referrers signal der Lichtschranke ausgeben
	}
	if (irio == 1 || ulio == 1)
	{
		uart_send_string("\n\r");				// Zeielnumbruch
		_delay_ms(1);
	}
	return 0;
}

int Sleep_mode(void) // µC in Sleep mode setzen
{
	PORTC &= ~(1<<PC1);
	PORTB |= (1<<PB0);					// Schrittmotor Endstufe DIESABLE
	Motor_richtung(5,5);				// uebergabe an Motor_richtung
	set_sleep_mode(SLEEP_MODE_IDLE);	// sleep mode Aktiviren
	sleep_mode();						// uC geht in Ideln
	return 0;
}

int Sensor_steuerung(int input)
{
	if (input == 1) // Starte oder stoppe Ultraschall radar
	{
		if (ulio == 0)
		{
			ulio = 1;
		}
		else
		{
			ulio = 0;
		}
	}
	if (input == 2) // Starte oder Stoppe Infrarot ausgabe
	{
		if (irio == 0)
		{
			irio = 1;
		}
		else
		{
			irio = 0;
		}
	}
	return 0;
}

int main(void)
{
	uart_init();						// Serial Inizialisirung
	DDRC = 0b01111111;
	DDRB = 0b11111111;
	DDRA = 0b11110001;
	DDRD &= ~((1 << PD2)|(1<<PD6));		// INT0 und Schrittmotor Endstop input...
	DDRD |= (1<<PD4)|(1<<PD5);			// PWM Ausgaenge festlegen
	ADCSRA = 0b10000111;				// Prescaler 128
	ADMUX |= (1<<REFS0);				// 5V Referrens spannung
	TCCR1A |= (1<<WGM10)|(1<<COM1A1)|(1<<COM1B1);
	TCCR1B |= (1<<WGM12)|(1<<CS12);		// Prescaler 256
	GICR |= (1<<INT0);					// IRS INT0 externer Interrupt aktiviren
	MCUCR |= (1<<ISC00);				// ISR INT0 Reaktion auf jede aenderung
	PORTB |= (1<<PB0);					// Schrittmotor Endstufe aus schalten
	PORTB &= ~(1<<PB2);					// Microstepps Disable
	PORTB |= (1<<PB6);					// Dir High
	PORTD |= (1<<PD6);					// Setze Pullup fuer Schrittmotor Endstop
	PORTD &= ~(1<<PD2);					// set pulldown for ISR Raspbarry PI check
	TIMSK |= (1<<TOIE0);				// Timer0 Overflow Interrupt erlauben
	
    while(1)
    {
		sei();						// Aktiviren aller interrups
		uart_init();				// Serial Inizialisirung
		if (rPI == 1)				// Wenn INT0 == High dann ...
		{
			PORTC |= (1<<PC1);
			Sensor_Ausgabe();		// Pereperie auswerten
			if (I_Wert == 49)		// Wenn eingabe == 49 dann ...
			{
				cli();						// Deaktiviren aller interrups
				I_Wert = 0;
				PORTC |= (1<<PC6);			// anzeigen das daten jetzt uebertragen werden koennen
				int Motor_R = (uart_get_int()-48);	// Richtungs vorgabe der Motoren 1-2 Vor-Rueckwaerts 5 = Motoren Aus
				int Motor_L = (uart_get_int()-48);	// Richtungs vorgabe der Motoren 3-4 Vor-Rueckwaerts 5 = Motoren Aus
				if(Motor_R > 5 || Motor_L > 5)		// Wenn eingabe groeßer als 5 dann ...
				{
					PORTC &= ~(1<<PC6);		// anzeigen das daten nicht mehr uebertragen werden koennen
					return main();			// Zurueck an denn anfang der main funktion
				}
				if(Motor_R == 5 || Motor_L == 5)	// Wenn eingabe == 5 dann ...
				{
					Motor_richtung(Motor_R,Motor_L);	// uebergabe an Motor_richtung
					PORTC &= ~(1<<PC6);			// anzeigen das daten nicht mehr uebertragen werden koennen
					return main();				// Zurueck an denn anfang der main funktion
				}
				int PWM[4] = {0,(uart_get_int()-48),(uart_get_int()-48),(uart_get_int()-48)};	// Annahmen der Motor geschwindigkein 0-255
				PWM[0] = (PWM[1]*100+PWM[2]*10+PWM[3]);
				int PWM1[4] = {0,(uart_get_int()-48),(uart_get_int()-48),(uart_get_int()-48)};	// Annahmen der Motor geschwindigkein 0-255
				PWM1[0] = (PWM1[1]*100+PWM1[2]*10+PWM1[3]);
				if (PWM[0] <= 255 && PWM1[0] <= 255)		// Wenn PWM kleiner als 255 dann ...
				{
					uart_send_string("MR: ");
					uart_send_int(Motor_R,1);
					uart_send_string(" ");
					uart_send_int(PWM[0],1);
					uart_send_string("\n\r");		// Sende zeielnumbruch
					uart_send_string("ML: ");
					uart_send_int(Motor_L,1);
					uart_send_string(" ");
					uart_send_int(PWM1[0],1);
					uart_send_string("\n\r");		// Sende zeielnumbruch
					if ((uart_get_int()-48) == 1)		// Bestaetigung der uebertragenen werte wenn eingabe == 1 dann ...
					{
						Motor_richtung(Motor_R,Motor_L);
						OCR1B = PWM[0];			// PWM setzen
						OCR1A = PWM1[0];		// PWM setzen
					}
				}
				PORTC &= ~(1<<PC6);		// anzeigen das daten nicht mehr uebertragen werden koennen
			}else
			{
				PORTC &= ~(1<<PC6);		// anzeigen das daten nicht mehr uebertragen werden koennen
			}
			if (I_Wert == 50)
			{
				cli();						// Deaktiviren aller interrups
				I_Wert = 0;
				PORTC |= (1<<PC6);			// anzeigen das daten jetzt uebertragen werden koennen
				int input = (uart_get_int()-48); //serielle eingabe
				Sensor_steuerung(input);
			}else
			{
				PORTC &= ~(1<<PC6);		// anzeigen das daten nicht mehr uebertragen werden koennen
			}
		}
		else
		{
			Sleep_mode();
		}
    }
}

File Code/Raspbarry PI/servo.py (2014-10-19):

#!/usr/bin/python

#--------------------
# Kamera Servo steuerung
# Autor: Jan-Tarek Butt
# Datum: 12.03.2014
#--------------------
import RPi.GPIO as GPIO
import time
import argparse

value = argparse.ArgumentParser(description='Servo Steuerung')
value.add_argument('integers', metavar='N', type=int,help='Wert fuer Servo postion')
args = value.parse_args()

# Pin 26 als Ausgang deklarieren
#GPIO.setwarnings(False)
GPIO.setmode(GPIO.BOARD)
GPIO.setup(26, GPIO.OUT)
# PWM mit 50Hz an Pin 26 starten
Servo = GPIO.PWM(26, 50)
Servo.start(0)
Servo.ChangeDutyCycle(args.integers)
time.sleep(0.5)
# PWM stoppen
Servo.stop()
GPIO.cleanup()

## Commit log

2014-08-20 add CAD construchtions
    [IR-Sensorhalter.fcstd, Rad_halterung.fcstd, Rad_halterung.stl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]
2014-08-20 remove some binary encoding
    [Rad_halterung_v2.stl, Radarhalterunge.stl, pi_cam_micro_servo_case.stl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]
2014-08-20 cange directory name and remove some binary encoding
    [IR-Sensorhalter.stl, Radarhalterunge_v1.stl, Rasberry_Halterung_A_v1.stl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]
2014-08-20 remove some binarys
    [IR-Sensorhalter.fcstd, Rad_halterung.fcstd, Radar_halterung.fcstd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]
2014-08-20 cange names and remove binarys
    [Radar_halterung.stl, Radar_halterung_v1.stl]
2014-09-18 fix motor control system
2014-09-25 add IR-Sensor holder on main construction
    [Roboter_Grundplatte.fcstd]
2014-09-26 svg file for Laser Cutted wheels
    [rad.fcstd, rad_v1.stl]
2014-09-27 worke on new Ultraschall Radar
    [Radar_halterung.fcstd, Radar_halterung.stl, Radar_halterung_v1.fcstd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]
2014-09-27 remove binarys
    [Ultraschall_Radar_Kopf.stl]
2014-09-28 add Ultraschall Radar kopplung
    [Ultraschall_Radar_Kopf.fcstd, Ultraschall_Radar_Kopf.stl, Ultraschall_Radar_Kopplung.fcstd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]
2014-10-01 fix enstop function for the steppermoter
    [Roboter.c]
2014-10-19 control sensor IO
2014-10-19 add servo control
